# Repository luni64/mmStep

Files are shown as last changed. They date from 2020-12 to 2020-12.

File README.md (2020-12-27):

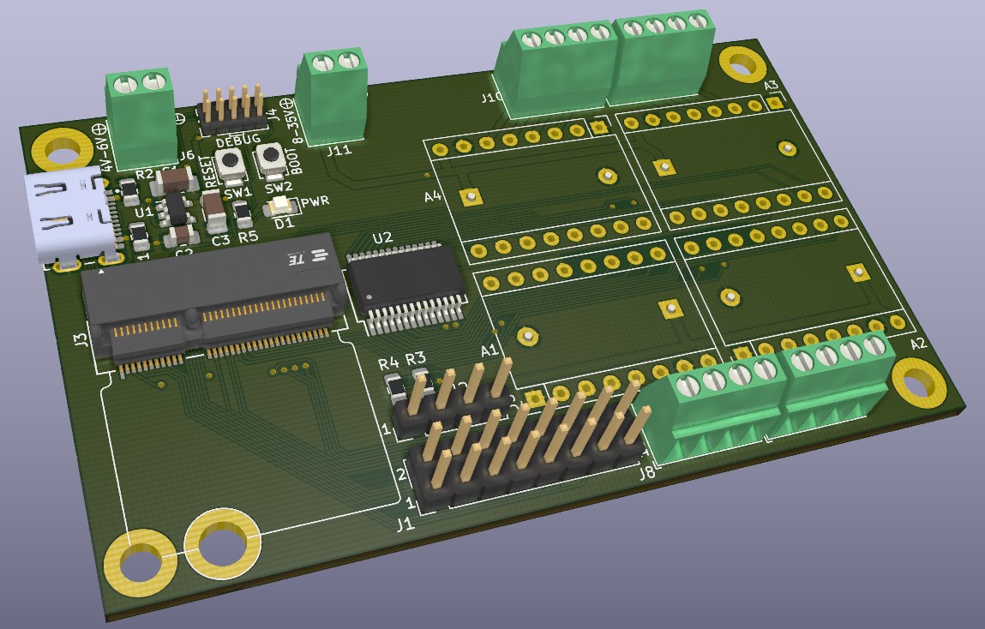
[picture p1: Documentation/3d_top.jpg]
3d top
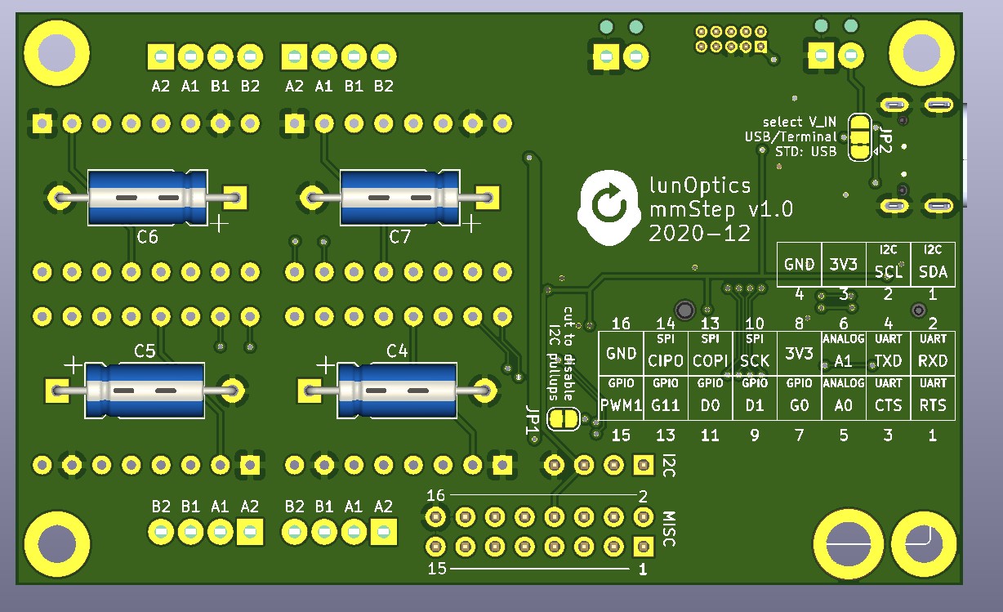
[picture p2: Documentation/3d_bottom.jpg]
3d bottom
 

# mmStep
Stepper driver board compatible to the SparkFun MicroMod system for DRV8825, A4988 etc. driver boards.

## Features:
- Up to 4 stepper driver modules with standard layout (DRV8825, A4988 etc.)
- V<sub>IN</sub> can be chosen from USB (standard) or an external (4-6V) supply
- V<sub>MOT</sub>:  8-35V
- Micro-step selection as well as enable are handled by a I2C multiplexer (MCP23017)
- STEP/DIR signals are directly connected to the GPIOs
- A couple of signals are broken out on pads (100 mil raster) to connect to the outside world (see silk screen on the bottom layer)
- Two layer, 81x49mm
- USB-C connector

## Production data
Here a [link](https://octopart.com/bom-tool/kZcnFrtS) to an Octopart BOM
containing live updated prices and availability from major distributors. It also
provides links to datasheets, and technical information and alternative parts.

Gerbers and drill files can be found in the [production](/Production) folder

Schematic, pictures, pinouts and datasheets can be found in the [documentation](/Documentation) folder.

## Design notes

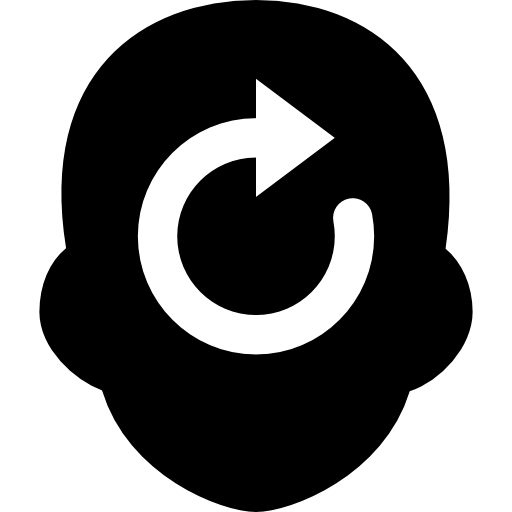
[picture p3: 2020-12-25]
KiCad/artwork/lunOptics.png

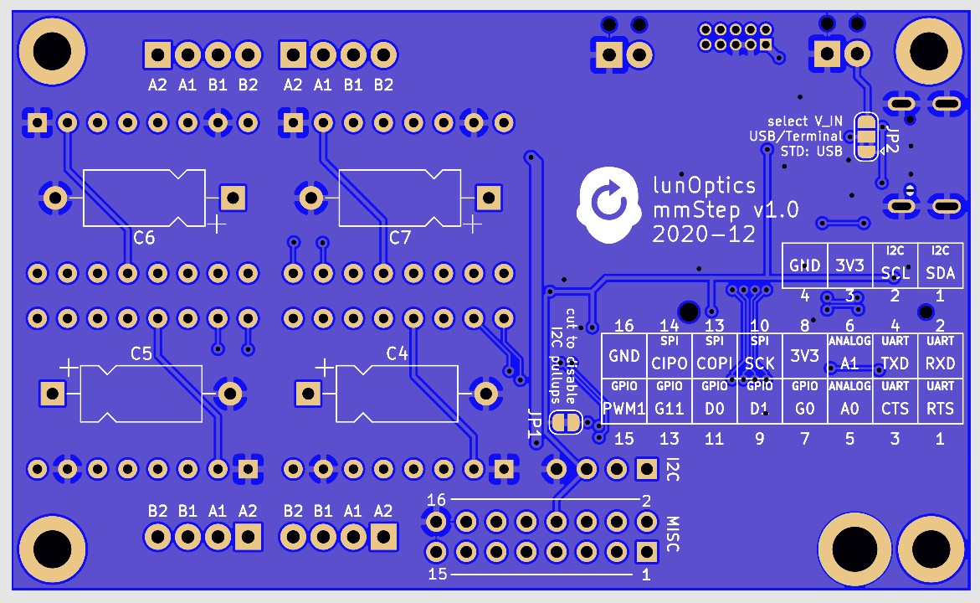
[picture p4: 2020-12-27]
Documentation/bottom layer.jpg

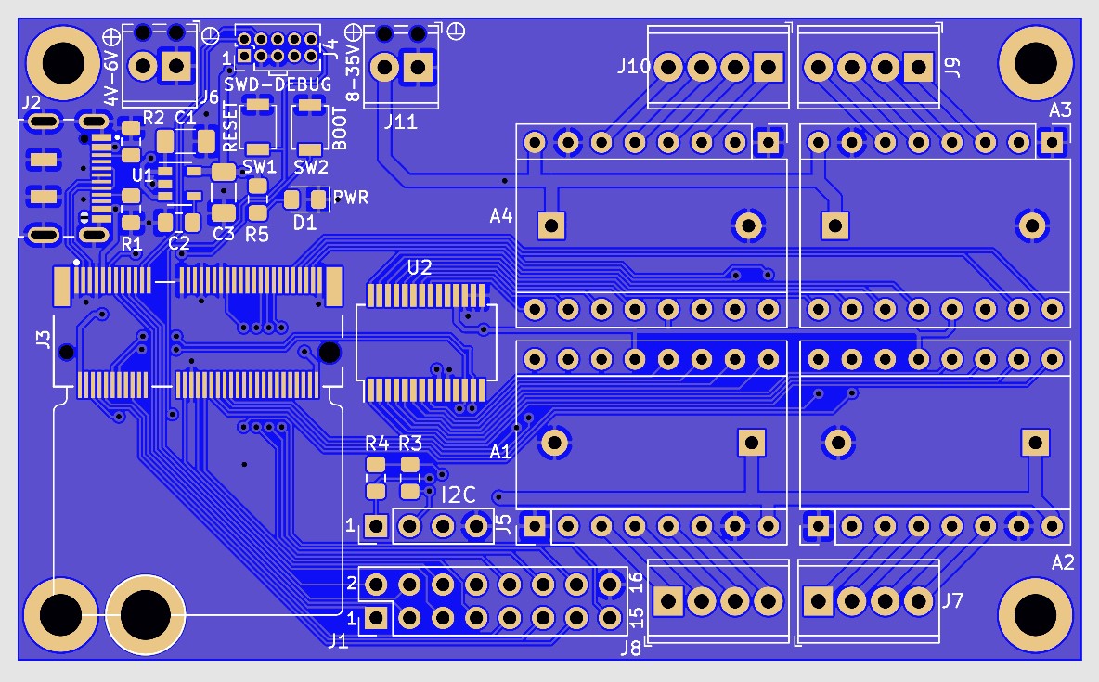
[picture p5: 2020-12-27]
Documentation/top layer.jpg

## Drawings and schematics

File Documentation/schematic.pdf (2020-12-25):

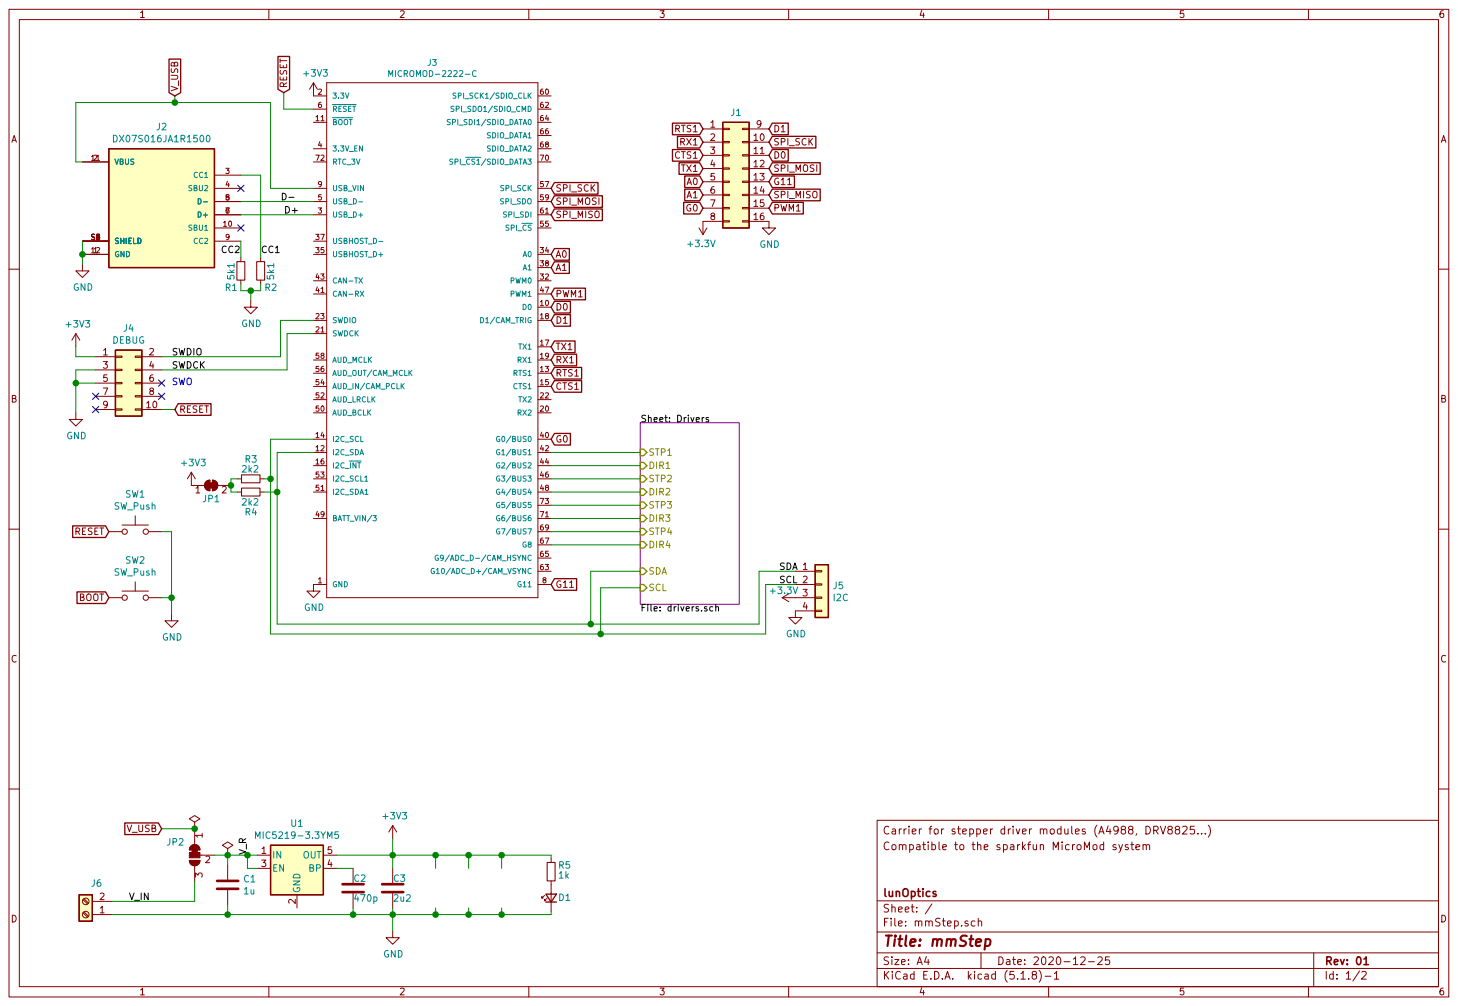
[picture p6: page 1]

Carrier for stepper driver modules (A4988, DRV8825...) Sheet: Drivers File: drivers.sch SDA

Compatible to the sparkfun MicroMod system

lunOptics
File: mmStep.sch Sheet: /
Id: 1/2 Title: mmStep

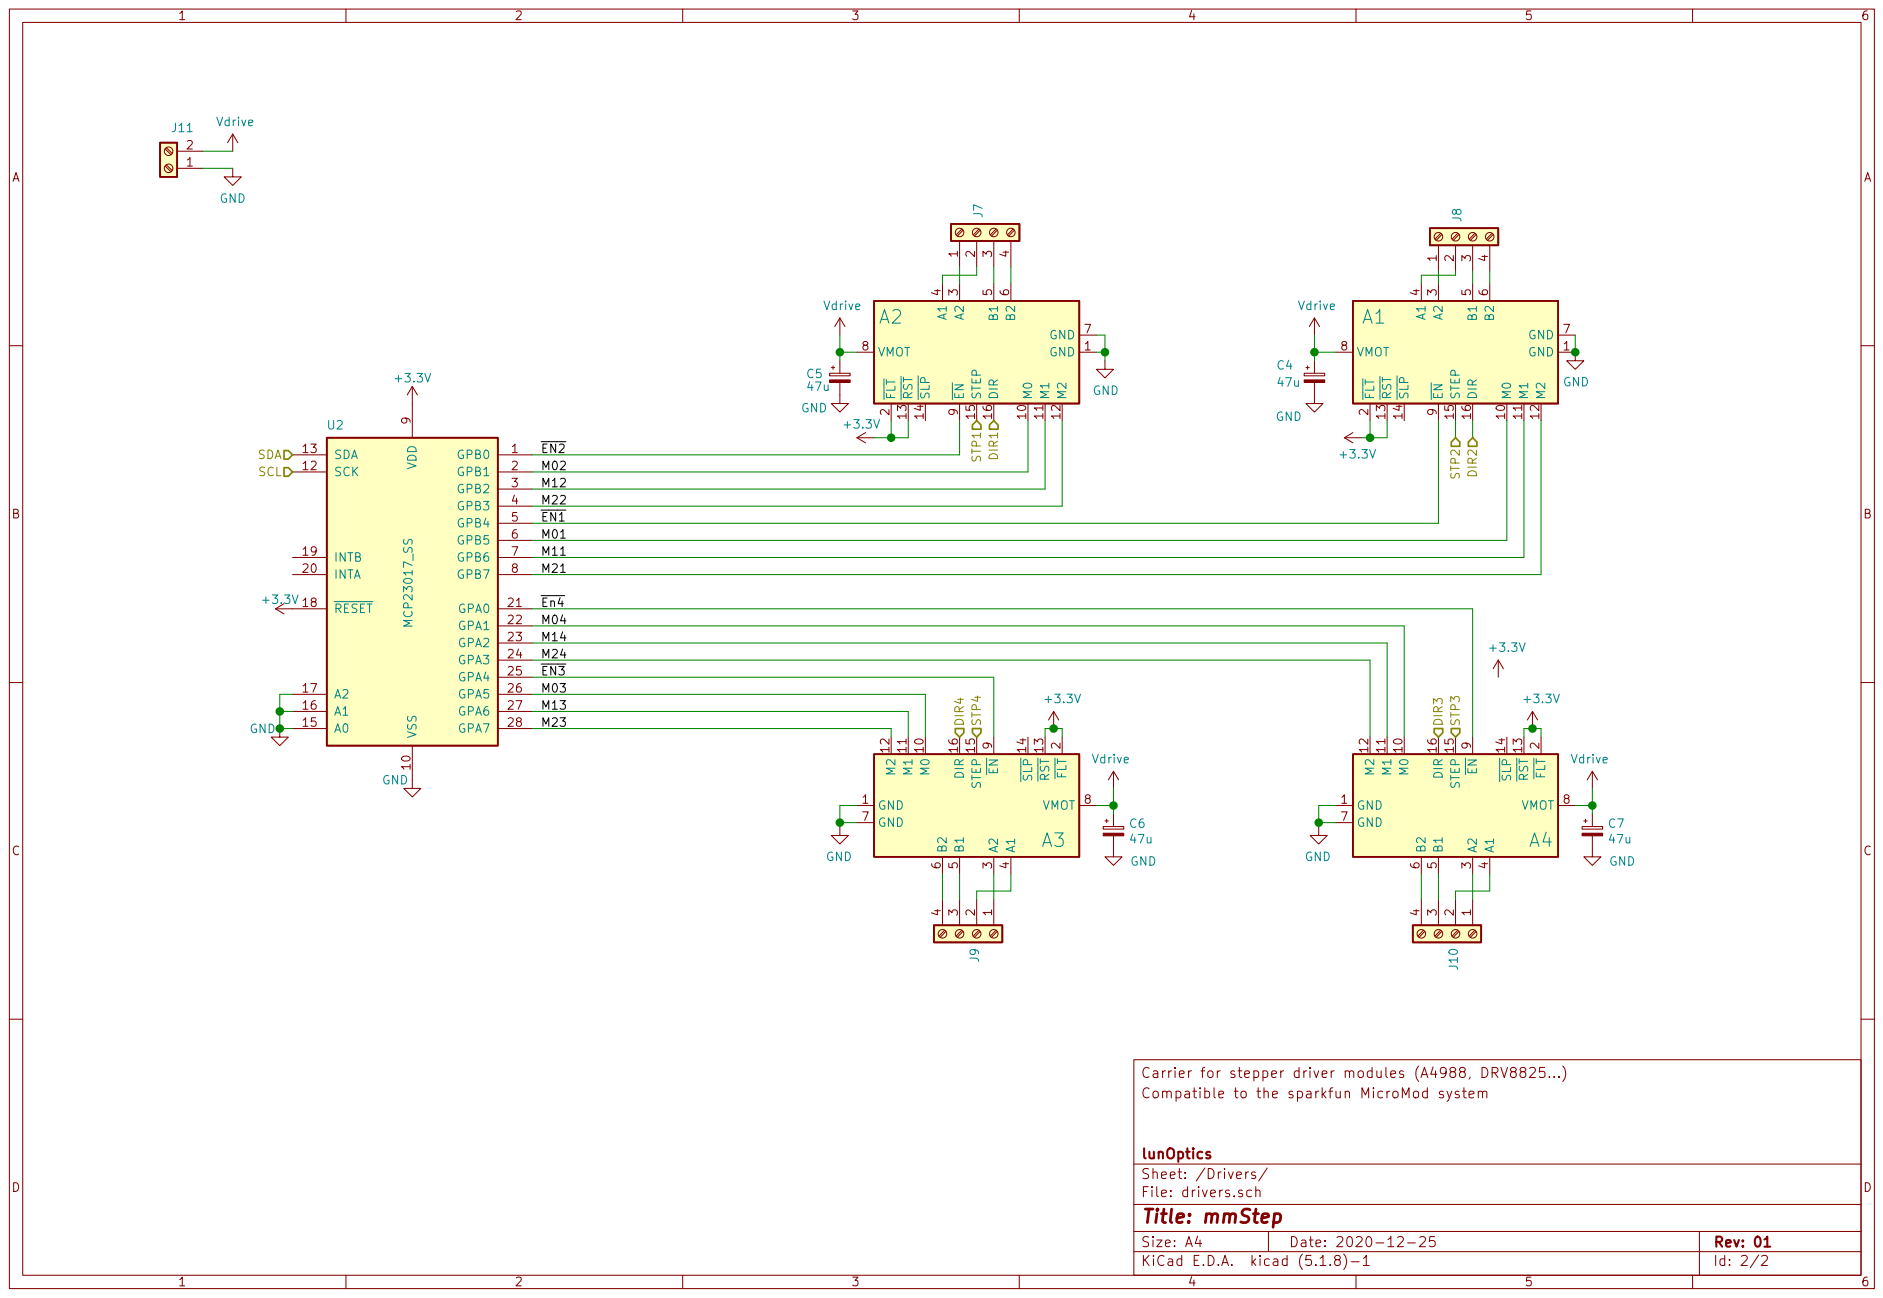
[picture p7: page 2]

4 J8 GND GND GPB0 +3.3V 1 VSS 10 SCK 12 SDA 13 A0 15 A1 16 A2 17 RESET 18

Carrier for stepper driver modules (A4988, DRV8825...) GND

Compatible to the sparkfun MicroMod system

lunOptics
File: drivers.sch Sheet: /Drivers/
Id: 2/2 Title: mmStep

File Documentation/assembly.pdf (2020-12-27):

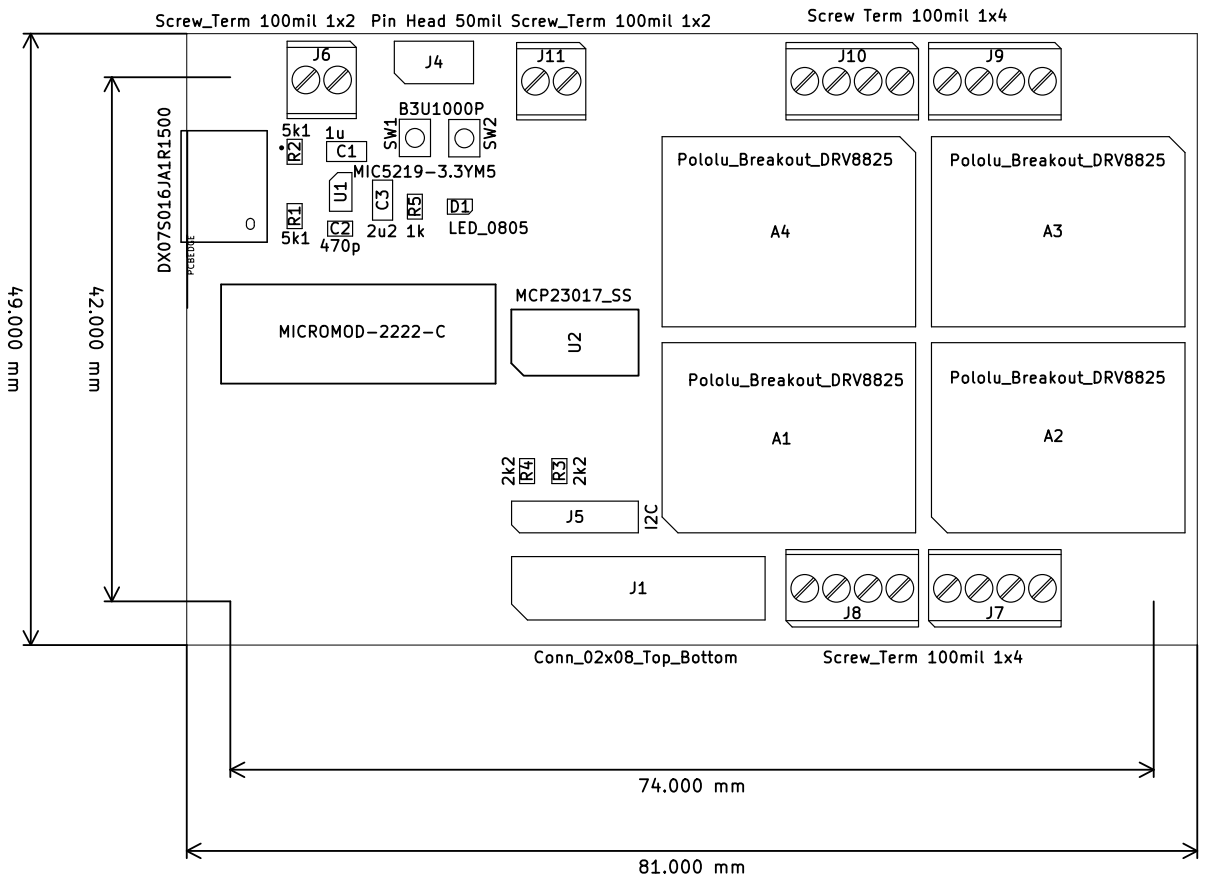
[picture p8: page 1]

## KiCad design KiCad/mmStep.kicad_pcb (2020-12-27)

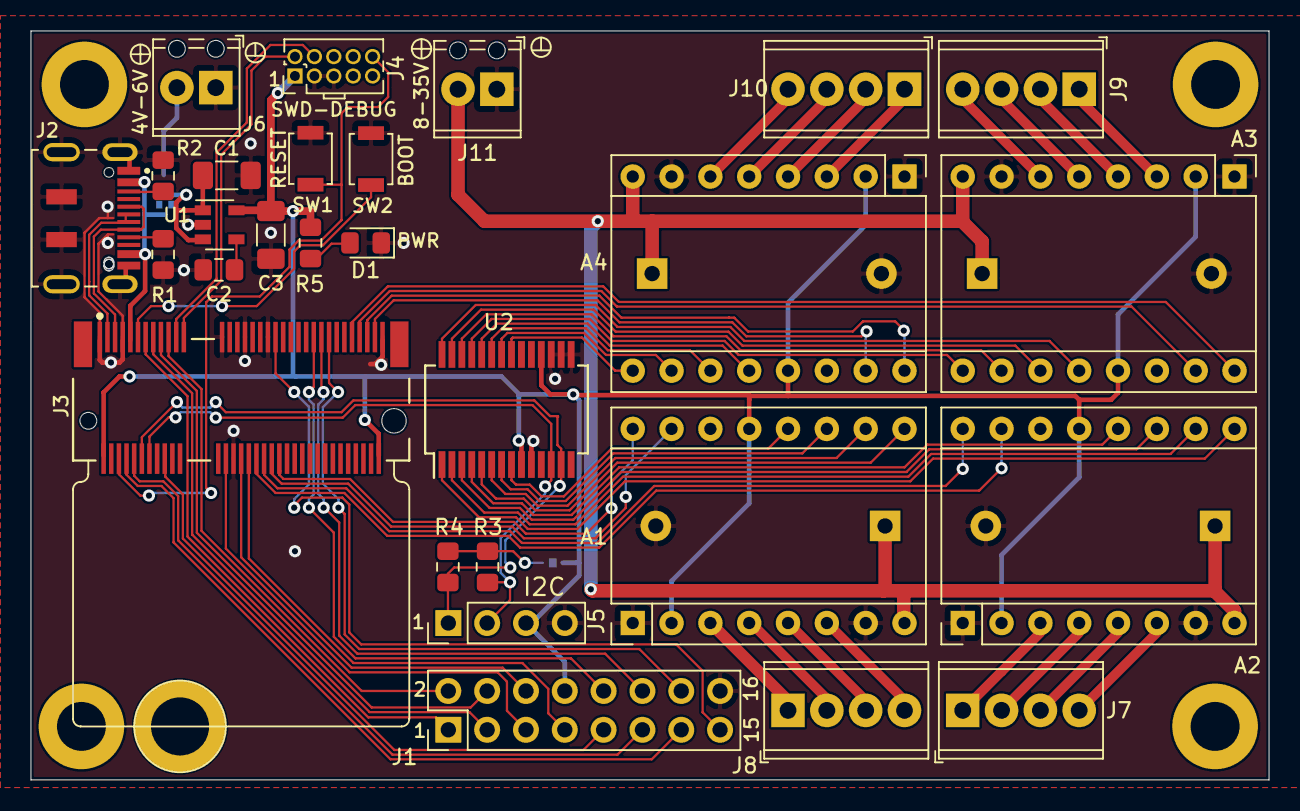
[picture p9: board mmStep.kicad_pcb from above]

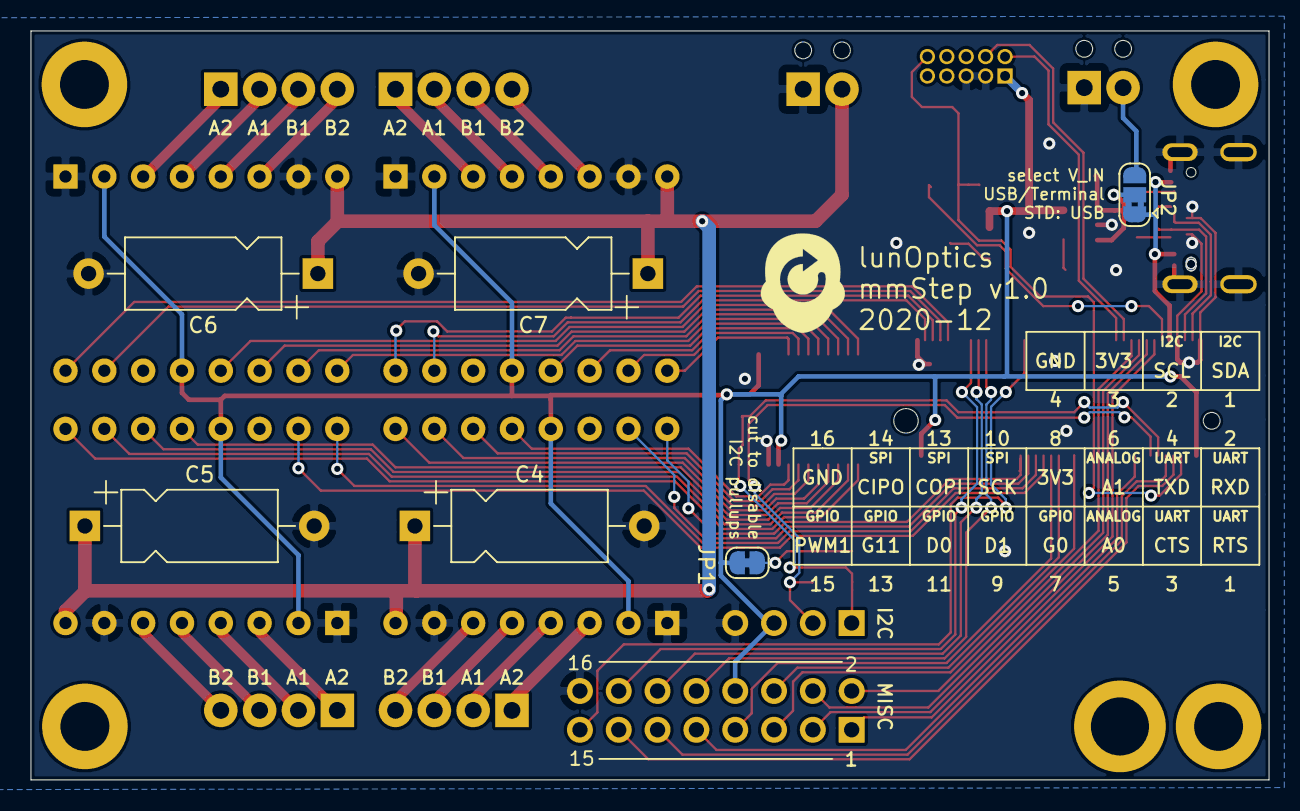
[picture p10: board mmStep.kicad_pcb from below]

Board: 2 copper layers, 81.0 x 49.0 mm, 34 parts (6 on the bottom side), 73 nets.

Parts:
A1, A2, A3, A4: Pololu_Breakout_DRV8825; Pololu_Breakout-16_15.2x20.3mm
C1: 1u; C_1206_3216Metric_Pad1.33x1.80mm_HandSolder
C2: 470p; C_0805_2012Metric_Pad1.15x1.40mm_HandSolder
C3: 2u2; C_1206_3216Metric_Pad1.33x1.80mm_HandSolder
C4, C5, C6, C7: 47u; CP_Axial_L10.0mm_D4.5mm_P15.00mm_Horizontal
D1: LED_0805; LED_0805_2012Metric_Pad1.15x1.40mm_HandSolder
J1: Conn_02x08_Top_Bottom; PinHeader_2x08_P2.54mm_Vertical
J2: DX07S016JA1R1500; JAE_DX07S016JA1R1500
J3: MICROMOD-2222-C; TE_Connectivity-2199230-4-Handsolder
J4: Pin Head 50mil; PinHeader_2x05_P1.27mm_Vertical
J5: I2C; PinHeader_1x04_P2.54mm_Vertical
J6, J11: Screw_Term 100mil 1x2; TerminalBlock_Phoenix_MPT-0,5-2-2.54_1x02_P2.54mm_Horizontal
J7, J9: Screw_Terminal_01x04; TerminalBlock_Phoenix_MPT-0,5-4-2.54_1x04_P2.54mm_Horizontal
J8: Screw_Term 100mil 1x4; TerminalBlock_Phoenix_MPT-0,5-4-2.54_1x04_P2.54mm_Horizontal
J10: Screw Term 100mil 1x4; TerminalBlock_Phoenix_MPT-0,5-4-2.54_1x04_P2.54mm_Horizontal
JP1: SolderJumper_2_Bridged; SolderJumper-2_P1.3mm_Bridged_RoundedPad1.0x1.5mm
JP2: SolderJumper_3_Bridged12; SolderJumper-3_P1.3mm_Bridged2Bar12_RoundedPad1.0x1.5mm
R1, R2: 5k1; R_0805_2012Metric_Pad1.15x1.40mm_HandSolder
R3, R4: 2k2; R_0805_2012Metric_Pad1.15x1.40mm_HandSolder
R5: 1k; R_0805_2012Metric_Pad1.15x1.40mm_HandSolder
SW1: B3U1000P; SW_SPST_B3U-1000P
SW2: SW_Push; SW_SPST_B3U-1000P
U1: MIC5219-3.3YM5; SOT-23-5
U2: MCP23017_SS; SSOP-28_5.3x10.2mm_P0.65mm

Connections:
+3V3: A1.2, A1.13, A2.2, A2.13, A3.2, A3.13, A4.2, A4.13, C3.1, J1.8, J3.2, J3.74, J4.1, J5.3, JP1.1, R5.1, U1.5, U2.9, U2.18
/CC1: J2.3, R2.1
/CC2: J2.9, R1.1
/D+: J2.6, J2.7, J3.3
/D-: J2.5, J2.8, J3.5
/Drivers/DIR1: A2.16, J3.44
/Drivers/DIR2: A1.16, J3.48
/Drivers/DIR3: A4.16, J3.71
/Drivers/DIR4: A3.16, J3.67
/Drivers/M01: A1.10, U2.6
/Drivers/M02: A2.10, U2.2
/Drivers/M03: A3.10, U2.26
/Drivers/M04: A4.10, U2.22
/Drivers/M11: A1.11, U2.7
/Drivers/M12: A2.11, U2.3
/Drivers/M13: A3.11, U2.27
/Drivers/M14: A4.11, U2.23
/Drivers/M21: A1.12, U2.8
/Drivers/M22: A2.12, U2.4
/Drivers/M23: A3.12, U2.28
/Drivers/M24: A4.12, U2.24
/Drivers/STP1: A2.15, J3.42
/Drivers/STP2: A1.15, J3.46
/Drivers/STP3: A4.15, J3.73
/Drivers/STP4: A3.15, J3.69
/Drivers/~EN1: A1.9, U2.5
/Drivers/~EN2: A2.9, U2.1
/Drivers/~EN3: A3.9, U2.25
/Drivers/~En4: A4.9, U2.21
/SCL: J3.14, J5.2, R3.1, U2.12
/SDA: J3.12, J5.1, R4.1, U2.13
/SWDCK: J3.21, J4.4
/SWDIO: J3.23, J4.2
/V_IN: J6.2, JP2.3
/V_R: C1.1, JP2.2, U1.1, U1.3
A0: J1.5, J3.34
A1: J1.6, J3.38
BOOT: J3.11, SW2.1
CTS1: J1.3, J3.15
D0: J1.11, J3.10
D1: J1.9, J3.18
G0: J1.7, J3.40
G11: J1.13, J3.8
GND: A1.1, A1.7, A2.1, A2.7, A3.1, A3.7, A4.1, A4.7, C1.2, C2.2, C3.2, C4.2, C5.2, C6.2, C7.2, D1.1, J1.16, J2.1, J2.12, J2.S1, J2.S2, J2.S3, J2.S4, J2.S5, J2.S6, J3.1, J3.7, J3.33, J3.36, J3.39, J3.45, J3.75, J4.3, J4.5, J5.4, J6.1, J11.1, R1.2, R2.2, SW1.2, SW2.2, U1.2, U2.10, U2.15, U2.16, U2.17
unnamed: A1.3, J8.1
unnamed: A1.4, J8.2
unnamed: A1.5, J8.3
unnamed: A1.6, J8.4
unnamed: A2.3, J7.1
unnamed: A2.4, J7.2
unnamed: A2.5, J7.3
unnamed: A2.6, J7.4
unnamed: A3.3, J9.1
unnamed: A3.4, J9.2
unnamed: A3.5, J9.3
unnamed: A3.6, J9.4
unnamed: A4.3, J10.1
unnamed: A4.4, J10.2
unnamed: A4.5, J10.3
unnamed: A4.6, J10.4
unnamed: C2.1, U1.4
unnamed: D1.2, R5.2
unnamed: JP1.2, R3.2, R4.2
PWM1: J1.15, J3.47
RESET: J3.6, J4.10, SW1.1
RTS1: J1.1, J3.13
RX1: J1.2, J3.19
SPI_MISO: J1.14, J3.61
SPI_MOSI: J1.12, J3.59
SPI_SCK: J1.10, J3.57
TX1: J1.4, J3.17
V_USB: J2.2, J2.11, J3.9, JP2.1
Vdrive: A1.8, A2.8, A3.8, A4.8, C4.1, C5.1, C6.1, C7.1, J11.2

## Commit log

2020-12-25 Fixed missing BOOT signal and some ERC errors
    [drivers.sch, mmStep.kicad_pcb, mmStep.sch]
2020-12-27 Added Gerbers and drill files
    [mmStep-B_Cu.gbr, mmStep-B_Mask.gbr, mmStep-B_Paste.gbp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]
